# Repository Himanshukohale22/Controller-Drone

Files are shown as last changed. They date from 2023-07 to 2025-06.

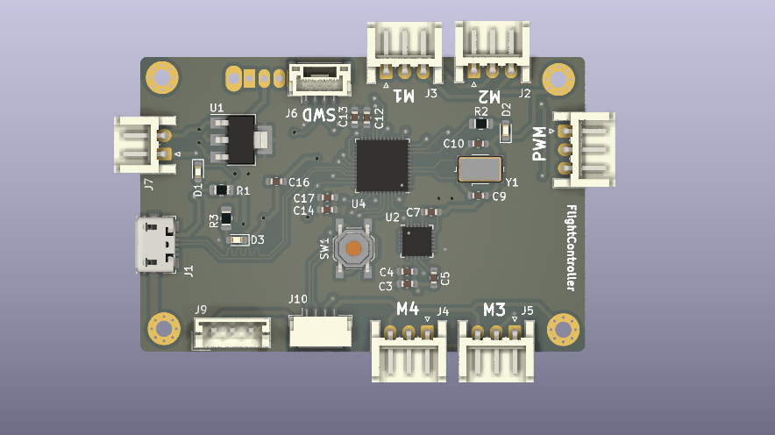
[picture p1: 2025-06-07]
Controller-Drone/images /Front-side.png.png

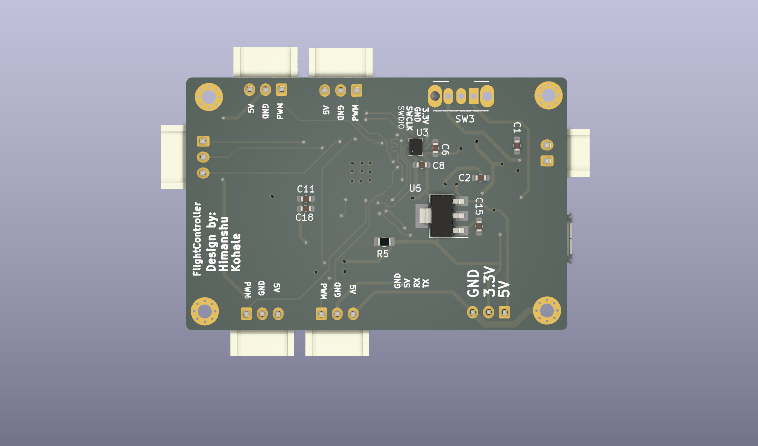
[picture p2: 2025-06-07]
Controller-Drone/images /Back-side.jpg.png

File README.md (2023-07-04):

# FLIGHT COMPUTER
controller for any four motors based flying object according to specification mentioned below.



This repository contains hardware files and gerber files of board . this is open source project board can be used aacording to features mentioned below.

### BOARD SPECIFICATION.
---

* STM32f4 cortex M4 based on board microcontroller for precision and fligt data simulation.
  * core -  Arm® 32-bit Cortex®-M4 CPU with FPU, Adaptive real-time accelerator .
  *  1 Mbyte of Flash memory
  *  192+4 Kbytes of SRAM
  *  Serial wire debug
* sensors
  * MPU9250.(IMU)
    *  9-axis of freedom. (6 are used).
    * accerelometer an gyroscopic values
    * Higher calibration precision.
    * for statbility and orientation of board/vehicle.
    * configured with SPI1.
  * BMP280 .(Barometer)
    * configured with I2C .
    * barometer for altitude calculations . helps to hover the flight.
    * absolutely accurate p = 950 -- 1100 hPa.
  * NRF module
    * nrf module for communication upto 1km.
    * configured with SPI2.
* for programme the ,board include four pins ckl , io , pwr , gnd as in 1.27mm pins(SWD). use ST-LINK.
* power input
  * usbB mini for testing testing.
  * jst connector i/p from 12v to 27v .

### schematics   
---





## 3D 
---





## Tools 

* [kicad](https://www.kicad.org/)

* [STM32cubeide](https://www.st.com/en/development-tools/stm32cubeide.html)

## Reference 
---

[stm32f411](https://www.st.com/resource/en/datasheet/stm32f411re.pdf)

[MPU6050](https://invensense.tdk.com/wp-content/uploads/2015/02/MPU-6000-Datasheet1.pdf)

[BMP280](https://cdn-shop.adafruit.com/datasheets/BST-BMP280-DS001-11.pdf)

[NRF24](https://www.sparkfun.com/datasheets/Components/SMD/nRF24L01Pluss_Preliminary_Product_Specification_v1_0.pdf)

## future work 
---
* work with higher level cortex controller.(ex f7/f8)
* include SD card for collecting flight data.
* include FVP cameras. and configuring. collecting photos/videos.
* higher level nrf modules for rf communications.

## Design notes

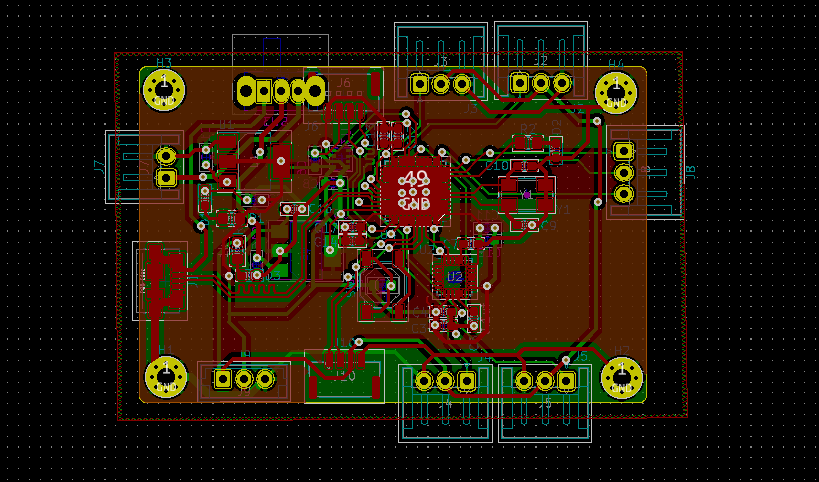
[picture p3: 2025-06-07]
Controller-Drone/images /PCB_LAYOUT.png.PNG

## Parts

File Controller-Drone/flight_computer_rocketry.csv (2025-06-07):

Id | Designator | Footprint | Quantity | Designation | Supplier and ref
1 | C14,C12,C17,C13,C11,C18 | C_0603_1608Metric_Pad1.08x0.95mm_HandSolder | 6 | 100pf
2 | D2 | LED_0603_1608Metric_Pad1.05x0.95mm_HandSolder | 1 | blue
3 | U1 | SOT-223-3_TabPin2 | 1 | AMS1117-3.3
4 | R2,R3,R1,R5 | R_0805_2012Metric_Pad1.20x1.40mm_HandSolder | 4 | 1k
5 | H3,H4,H2,H1 | MountingHole_2.2mm_M2_Pad_Via | 4 | MountingHole_Pad
6 | C3 | C_0603_1608Metric_Pad1.08x0.95mm_HandSolder | 1 | 10nf
7 | J1 | USB_Micro-B_Molex_47346-0001 | 1 | USB_B_Mini
8 | J10 | JST_GH_SM04B-GHS-TB_1x04-1MP_P1.25mm_Horizontal | 1 | Conn_01x04_Pin
9 | Y1 | Crystal_SMD_0603-4Pin_6.0x3.5mm | 1 | Crystal_GND23_Small
10 | U4 | QFN-48-1EP_7x7mm_P0.5mm_EP5.6x5.6mm | 1 | STM32F401CBUx
11 | C5,C4,C16,C2 | C_0603_1608Metric_Pad1.08x0.95mm_HandSolder | 4 | 0.1uf
12 | C10,C9 | C_0603_1608Metric_Pad1.08x0.95mm_HandSolder | 2 | 12pf
13 | J6 | JST_GH_BM04B-GHS-TBT_1x04-1MP_P1.25mm_Vertical | 1 | Conn_01x04_Pin
14 | SW1 | SW_SPST_TL3342 | 1 | SW_Push
15 | J3,J8,J4,J5,J2 | JST_EH_S3B-EH_1x03_P2.50mm_Horizontal | 5 | Conn_01x03_Male
16 | J9 | JST_EH_B3B-EH-A_1x03_P2.50mm_Vertical | 1 | Conn_01x03_Male
17 | J7 | JST_EH_S2B-EH_1x02_P2.50mm_Horizontal | 1 | Conn_01x02_Male
18 | D1 | LED_0603_1608Metric_Pad1.05x0.95mm_HandSolder | 1 | GREEN
19 | U2 | InvenSense_QFN-24_4x4mm_P0.5mm | 1 | MPU-6050
20 | C7 | C_0603_1608Metric_Pad1.08x0.95mm_HandSolder | 1 | 2.2nf
21 | D3 | LED_0603_1608Metric_Pad1.05x0.95mm_HandSolder | 1 | RED
22 | SW3 | SW_CuK_OS102011MA1QN1_SPDT_Angled | 1 | SW_SPDT
23 | U3 | Bosch_LGA-8_2x2.5mm_P0.65mm_ClockwisePinNumbering | 1 | BMP280
24 | C8,C6 | C_0603_1608Metric_Pad1.08x0.95mm_HandSolder | 2 | 100nf
25 | C1,C15 | C_0603_1608Metric_Pad1.08x0.95mm_HandSolder | 2 | 10uf
26 | U5 | SOT-223-3_TabPin2 | 1 | L7805

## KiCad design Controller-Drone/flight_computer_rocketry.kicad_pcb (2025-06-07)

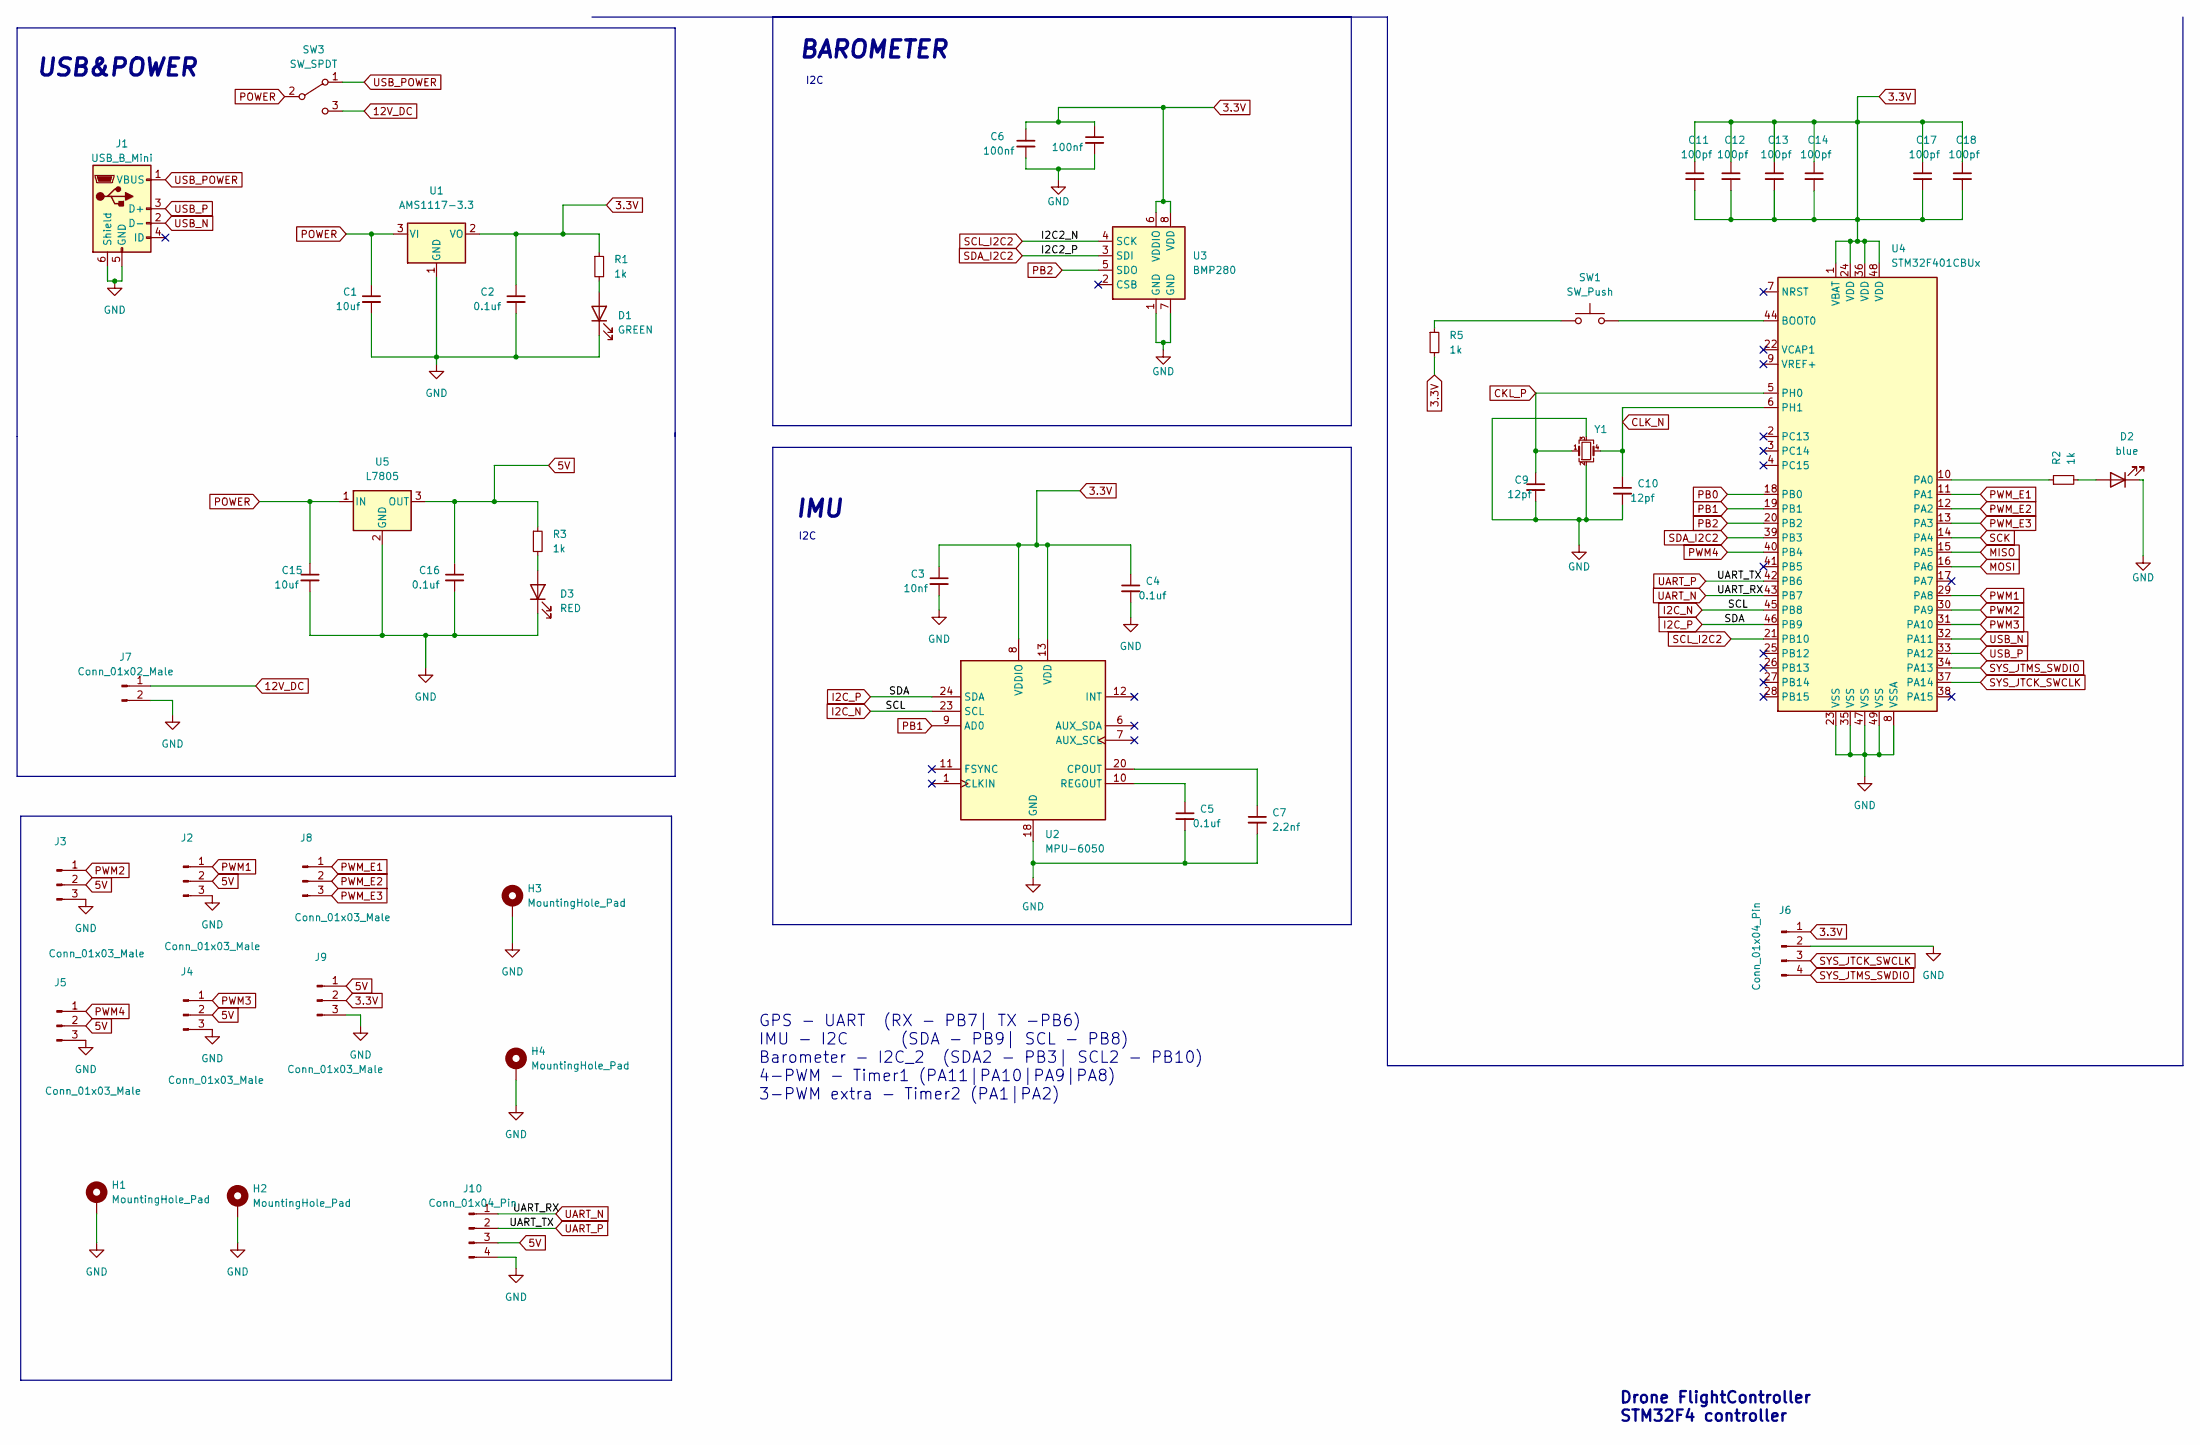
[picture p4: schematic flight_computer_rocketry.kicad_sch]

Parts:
C1, C15: 10uf; C_0603_1608Metric_Pad1.08x0.95mm_HandSolder
C2, C4, C5, C16: 0.1uf; C_0603_1608Metric_Pad1.08x0.95mm_HandSolder
C3: 10nf; C_0603_1608Metric_Pad1.08x0.95mm_HandSolder
C6, C8: 100nf; C_0603_1608Metric_Pad1.08x0.95mm_HandSolder
C7: 2.2nf; C_0603_1608Metric_Pad1.08x0.95mm_HandSolder
C9, C10: 12pf; C_0603_1608Metric_Pad1.08x0.95mm_HandSolder
C11, C12, C13, C14, C17, C18: 100pf; C_0603_1608Metric_Pad1.08x0.95mm_HandSolder
D1: GREEN; LED_0603_1608Metric_Pad1.05x0.95mm_HandSolder
D2: blue; LED_0603_1608Metric_Pad1.05x0.95mm_HandSolder
D3: RED; LED_0603_1608Metric_Pad1.05x0.95mm_HandSolder
H1, H2, H3, H4: MountingHole_Pad; MountingHole_2.2mm_M2_Pad_Via
J1: USB_B_Mini; USB_Micro-B_Molex_47346-0001
J2, J3, J4, J5, J8: Conn_01x03_Male; JST_EH_S3B-EH_1x03_P2.50mm_Horizontal
J6: Conn_01x04_Pin; JST_GH_BM04B-GHS-TBT_1x04-1MP_P1.25mm_Vertical
J7: Conn_01x02_Male; JST_EH_S2B-EH_1x02_P2.50mm_Horizontal
J9: Conn_01x03_Male; JST_EH_B3B-EH-A_1x03_P2.50mm_Vertical
J10: Conn_01x04_Pin; JST_GH_SM04B-GHS-TB_1x04-1MP_P1.25mm_Horizontal
R1, R2, R3, R5: 1k; R_0805_2012Metric_Pad1.20x1.40mm_HandSolder
SW1: SW_Push; SW_SPST_TL3342
SW3: SW_SPDT; SW_CuK_OS102011MA1QN1_SPDT_Angled
U1: AMS1117-3.3; SOT-223-3_TabPin2
U2: MPU-6050; InvenSense_QFN-24_4x4mm_P0.5mm
U3: BMP280; Bosch_LGA-8_2x2.5mm_P0.65mm_ClockwisePinNumbering
U4: STM32F401CBUx; QFN-48-1EP_7x7mm_P0.5mm_EP5.6x5.6mm
U5: L7805; SOT-223-3_TabPin2
Y1: Crystal_GND23_Small; Crystal_SMD_0603-4Pin_6.0x3.5mm

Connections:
3.3V: C2.1, C3.1, C4.1, C6.1, C8.1, C11.1, C11.2, C12.1, C12.2, C13.1, C13.2, C14.1, C14.2, C17.1, C17.2, C18.1, C18.2, J6.1, J9.2, R1.1, R5.2, U1.2 (VO), U2.8 (VDDIO), U2.13 (VDD), U3.6 (VDDIO), U3.8 (VDD), U4.1 (VBAT), U4.24 (VDD), U4.36 (VDD), U4.48 (VDD)
5V: C16.1, J2.2, J3.2, J4.2, J5.2, J9.1, J10.3, R3.1, U5.3 (OUT)
12V_DC: J7.1, SW3.3 (C)
CKL_P: C9.1, U4.5 (PH0), Y1.1
CLK_N: C10.1, U4.6 (PH1), Y1.4
GND: C1.2, C2.2, C3.2, C4.2, C5.2, C6.2, C7.2, C8.2, C9.2, C10.2, C15.2, C16.2, D1.1 (K), D2.1 (K), D3.1 (K), H1.1, H2.1, H3.1, H4.1, J1.5 (GND), J1.6 (Shield), J2.3, J3.3, J4.3, J5.3, J6.2, J7.2, J9.3, J10.4, U1.1 (GND), U2.18 (GND), U3.1 (GND), U3.7 (GND), U4.8 (VSSA), U4.23 (VSS), U4.35 (VSS), U4.47 (VSS), U4.49 (VSS), U5.2 (GND), Y1.2, Y1.3
I2C_N: U2.23 (SCL), U4.45 (PB8)
I2C_P: U2.24 (SDA), U4.46 (PB9)
MISO: U4.15 (PA5)
MOSI: U4.16 (PA6)
unnamed: D1.2 (A), R1.2
unnamed: D2.2 (A), R2.2
unnamed: D3.2 (A), R3.2
unnamed: R5.1, SW1.1
unnamed: C7.1, U2.20 (CPOUT)
unnamed: C5.1, U2.10 (REGOUT)
unnamed: SW1.2, U4.44 (BOOT0)
unnamed: R2.1, U4.10 (PA0)
PB0: U4.18 (PB0)
PB1: U2.9 (AD0), U4.19 (PB1)
PB2: U3.5 (SDO), U4.20 (PB2)
POWER: C1.1, C15.1, SW3.2 (B), U1.3 (VI), U5.1 (IN)
PWM1: J2.1, U4.29 (PA8)
PWM2: J3.1, U4.30 (PA9)
PWM3: J4.1, U4.31 (PA10)
PWM4: J5.1, U4.40 (PB4)
PWM_E1: J8.1, U4.11 (PA1)
PWM_E2: J8.2, U4.12 (PA2)
PWM_E3: J8.3, U4.13 (PA3)
SCK: U4.14 (PA4)
SCL_I2C2: U3.4 (SCK), U4.21 (PB10)
SDA_I2C2: U3.3 (SDI), U4.39 (PB3)
SYS_JTCK_SWCLK: J6.3, U4.37 (PA14)
SYS_JTMS_SWDIO: J6.4, U4.34 (PA13)
UART_N: J10.1, U4.43 (PB7)
UART_P: J10.2, U4.42 (PB6)
USB_N: J1.2 (D-), U4.32 (PA11)
USB_P: J1.3 (D+), U4.33 (PA12)
USB_POWER: J1.1 (VBUS), SW3.1 (A)

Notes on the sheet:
I2C
GPS - UART (RX - PB7| TX -PB6) IMU - I2C (SDA - PB9| SCL - PB8) Barometer - I2C_2 (SDA2 - PB3| SCL2 - PB10) 4-PWM - Timer1 (PA11|PA10|PA9|PA8) 3-PWM extra - Timer2 (PA1|PA2)
IMU
Drone FlightController STM32F4 controller
USB&POWER
BAROMETER

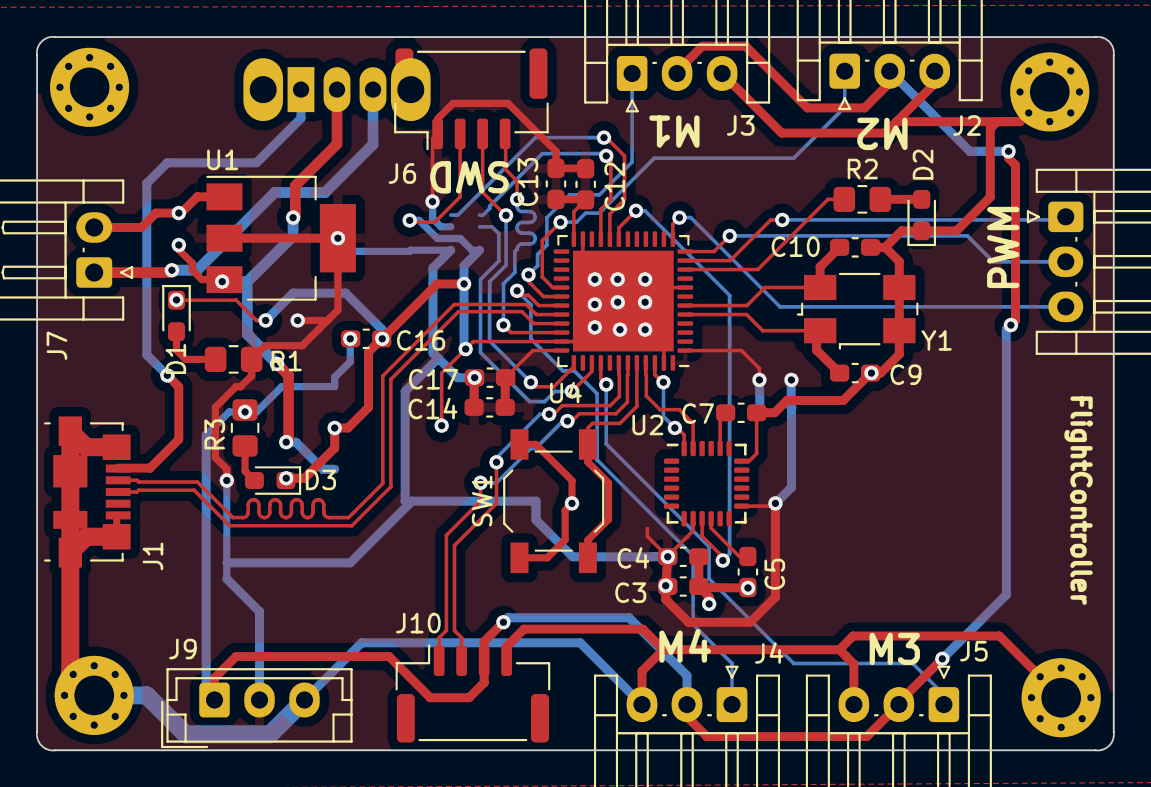
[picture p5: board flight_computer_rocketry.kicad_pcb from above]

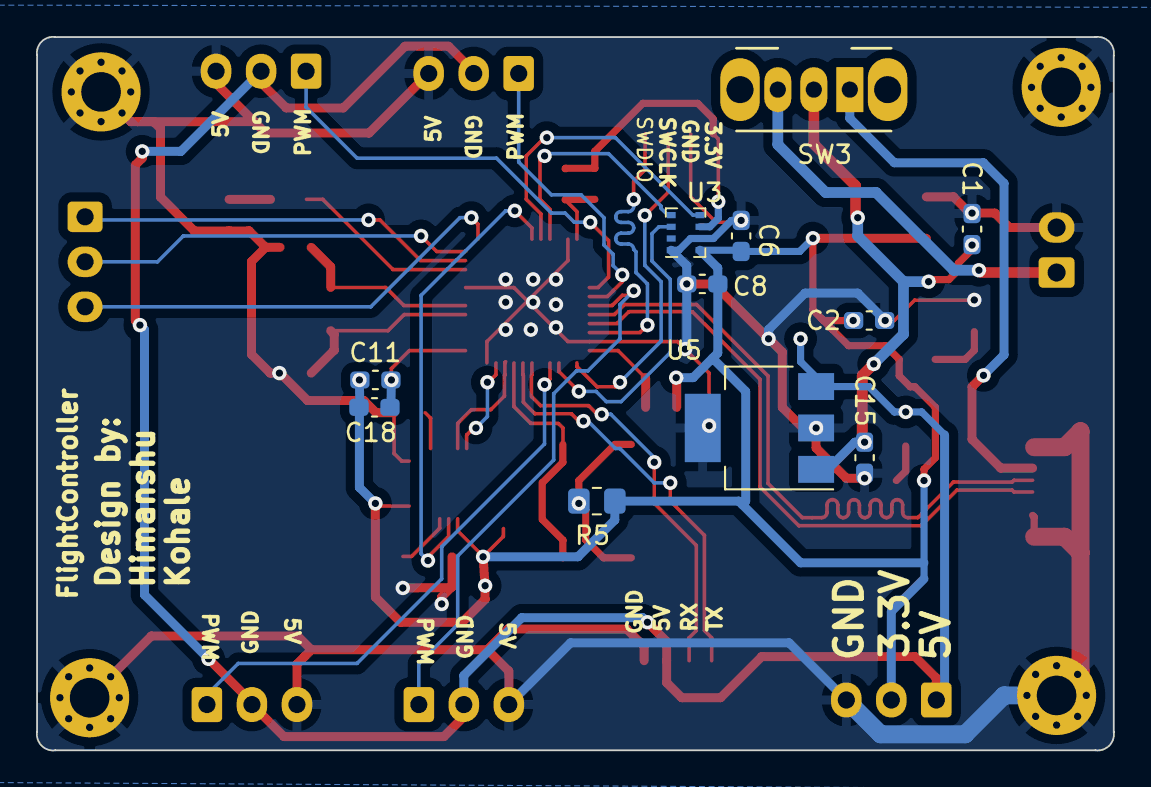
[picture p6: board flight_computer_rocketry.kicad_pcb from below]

Board: 2 copper layers, 59.8 x 39.6 mm, 47 parts (11 on the bottom side), 35 nets.

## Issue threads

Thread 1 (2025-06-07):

updated desing for the same

Himanshukohale22, 2025-06-07:
Update new desing for same
1. Desing size
2. GPS  support
3. Extra PWM

please find desing with repo and add issues with requirments
Thanks

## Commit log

2023-07-04 schematics added
2025-06-07 adding hardware files and images
    [flight_computer_rocketry-B_Cu.gbr, flight_computer_rocketry-B_Mask.gbr, flight_computer_rocketry-B_Paste.gbr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]
